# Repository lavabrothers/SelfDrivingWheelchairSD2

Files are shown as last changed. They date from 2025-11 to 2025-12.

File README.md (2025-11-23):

# SmartStride

Watch the video (https://youtu.be/vgjbnsrbdY0?si=ctMS2qIhK_sTW9yw)

*A quick, informal video showcasing the project.*

## Overview

SmartStride is an affordable, easy to use mobility upgrade system designed to retrofit existing electric wheelchairs with autonomous capabilities. The system integrates a Raspberry Pi 5-based control unit that processes data from a IMU and an infrared depth sensor (Kinect V2) to enable real-time obstacle detection and navigation. The goal of this project is to improve the mobility and overall safety of users with limited body control through intelligent motion assistance, all while maintaining an affordable cost and an easy-to-implement modular design. We designed the system around the Kinect V2, an inexpensive sensor array that is quite powerful compared to other sensors of its weight class. A good example is hospital settings moving patients around.

## Features

The system offers several modes of operation, controlled via a custom ESP32-based wireless controller:

- **Follow Person:** Using the Kinect's camera, the wheelchair will identify and follow the torso of an individual.
- **Autocruise:** The wheelchair cruises forward at a steady pace and stops promptly if an object obstructs its path. Once the path is clear, it continues cruising.
- **Manual Control:** Reverts to standard joystick operation, allowing the wheelchair to be driven manually, just as it was originally designed.
- **Mapping:** Utilizes the Kinect sensor's IR Flood Sensor to generate a 3D point cloud map of the surroundings by rotating the chair 360°.

## System Architecture

### Hardware

The system is built around a Raspberry Pi 5 as the central processing unit, which coordinates sensor inputs and motor controls.

- **Central Processing Unit:** Raspberry Pi 5
- **Depth Sensing & Vision:** Microsoft Kinect V2
- **Wireless Control:** ESP32-based controller with joystick
- **Orientation & Motion Tracking:** MPU-9250 (3-axis gyroscope, magnetometer, accelerometer)
- **Digital-to-Analog Conversion:** MCP4728 DAC to interface with the wheelchair's joystick port.
- **Power & Interfacing:** Four custom-designed PCBs for voltage regulation (12V, 5V, 3.3V) and comprehensive connectivity between all components via I2C

### Software

The software architecture is designed for dual-mode control, enabling both manual and autonomous operation.

- **Kinect Interfacing:** The open-source `libfreenect2` library is used to interface with the Kinect V2 sensor, providing high-definition color (RGB) streams, an infrared stream, and a Time-of-Flight (ToF) depth map.
- **Control Logic:** The Raspberry Pi runs scripts to handle both autonomous and manual control. In manual mode, it processes Bluetooth commands from the ESP32. In autonomous mode, it uses data from the Kinect to navigate and avoid obstacles.

## Installation

### Raspberry Pi (Wheelchair Side)

Follow these steps to set up the software on the Raspberry Pi.

1.  **Clone the Repository:**
    ```bash
    git clone https://github.com/lavabrothers/SelfDrivingWheelchairSD2.git
    cd SelfDrivingWheelchairSD2
    ```

2.  **Install `libfreenect2` (Kinect Driver):**
    The Kinect sensor requires the `libfreenect2` driver. Please follow the official installation instructions at [https://github.com/OpenKinect/libfreenect2](https://github.com/OpenKinect/libfreenect2).

3.  **Set Up the Python Environment:**
    Navigate to the `pi-code` directory to set up the Python environment.
    ```bash
    cd pi-code
    ```
    Create and activate a virtual environment (Make sure its Python3.11 or Python3.12):
    ```bash
    python3 -m venv .venv
    source .venv/bin/activate
    ```

4.  **Install Dependencies:**

    First, install the remaining packages from `requirements.txt`.
    ```bash
    pip install -r requirements.txt
    ```

    Next, install `pylibfreenect2` directly from the git repository, as it requires a special installation step.
    ```bash
    pip install git+https://github.com/r9y9/pylibfreenect2.git@40221e815c182ee31e8da33df717ccdef1bc615f
    ```

    *Note: If the above command fails, you may need to check if you installed libfreenect2 correctly. Sometimes you need to make sure the proper enviroment varaibles are set for your enviroment*

5.  **Install and Run the Service:**
    Navigate back to the root directory and use the `servicescript.sh` to install and start the main application as a systemd service. This will ensure it runs automatically on boot.
    ```bash
    cd ..
    sudo ./servicescript.sh install
    ```
    You can check the status of the service at any time with:
    ```bash
    sudo ./servicescript.sh status
    ```

## The Team

- **Matthew Itskovich:** Computer Engineering: Designed the ESP32 Code and Controller hardware
- **Evan Rees:** Computer Engineering: Designed Python Code and was Team Lead
- **Adam Lilly:** Electrical Engineering: Designed and Manufactured Regulators
- **Arturo Lara:** Computer Engineering: Admin Content and Soldering

## Project Media

**Longer, more detailed video:**
Watch the video (https://youtu.be/YJEAqcdVi9I?si=8ahl_1vFBt-6s-wN)

## Documentation

For more in-depth information, please refer to the following documents:

- **[Senior Design Conference Paper](./Documentation/Senior%20Design%20Conference%20Paper.pdf)**
- Additional written work on how this project works can be found in the `Documentation` folder.

## Map Example

**Demo Day Map:**
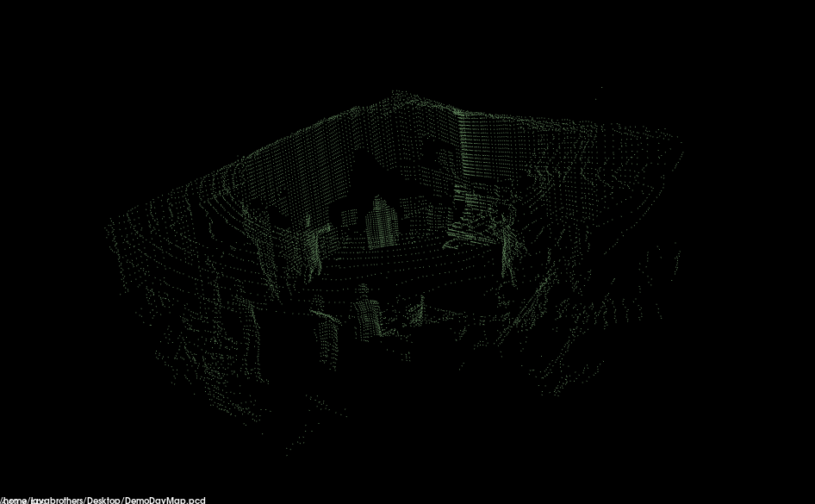
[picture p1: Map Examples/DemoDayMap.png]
Demo Day Map


## Acknowledgements

We would like to thank Dr. Chung Yong Chan and Dr. Arthur Weeks for their guidance and feedback throughout the SmartStride project. Their support and mentorship were invaluable in shaping the direction, design process, and successful completion of this project.

Thank you Dr.Wei for providing the wheelchair for use in this project.

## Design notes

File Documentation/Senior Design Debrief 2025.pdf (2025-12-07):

# Senior Design Fall 2025 Debrief

Hello! If your reading this then you have been given this wheelchair probably by Dr. Wei as a Senior Design Project for the future! My Name is Evan Rees and this was the first year we utilized and repaired this chair, so here are some lessons we learned that you can use in your iteration of a project!

Before I go into it too much, here is my contact information:
Email: ev596984@ucf.edu / evan@thereesgroup.com
Phone: +1 (941)-465-8774

If you every need some help getting antiquated or have a question that isn’t too easy to solve, shoot me a text/email and I will get back to you if I have a solution. No promises as I’m a student just like you and made a ton of mistakes and this chair still has a few unknowns. If we had more than two semesters then we maybe would have figured them all out ;]

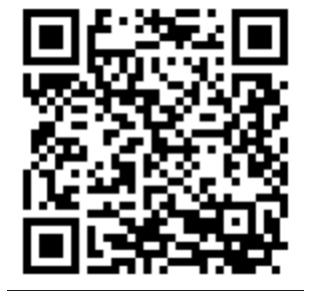
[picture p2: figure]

### SMART-STRIDE

This was our project for Summer/Fall 2025, you can access our website at: http://maverick.eecs.ucf.edu/seniordesign/su2025fa2025/g11/
or if that’s not your fancy we have a GitHub here: https://github.com/lavabrothers/SelfDrivingWheelchairSD2

Long story short we designed the wheelchair to move wireless and somewhat autonomously powered by a Pi 5, a 4 output DAC, and a Kinectv2 Sensor. All the code is made with these elements in mind, with a ESP32 as a wireless controller. It contains 4 modes:

- Wireless Manual Control Mode
- This mode basically just sends joystick inputs to the wheelchair, as if it’s plugged in directly
- Cruise Control Mode

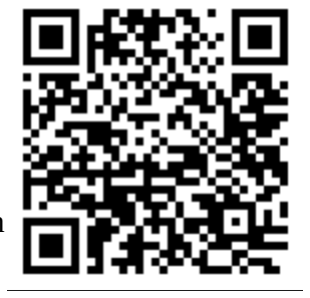
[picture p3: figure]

- This drives forward and will stop if it detects anything too close such an an object or a wall
- Follow Mode
- This will identify the closest person to the wheelchair, and attempt to
maintain distance from the person and keep them centered in it’s vision
- Map Mode
- This will spin the wheelchair 360 degrees and construct a depthmap of the environment around it

The GitHub has the most up to date info, but the website can get you an idea on how we progressed over the Senior Design Class. I recommend if you setup something similar, go to commit 22fafa5 as that has a bunch of crummy dev scripts you can use to test and experiment. However the repo is built in a way to do most everything already.

At time of writing I’m not sure if Dr. Wei will have you start your own project, or jump off the work we have already done, but if it’s the latter I have some ideas for you:

QR Code: GitHub

QR Code: Website

IDEAS
- Utilize the unused map mode to stitch together larger environments
- Fix follow mode to be more reliable and follow a single person without being stolen by another close person
- Assisted Manual Control that will help the user avoid obstacles while in manual mode
- Utilizing a rejected voice control mode (read back in the code commits), enable voice controls
- Integrate AI of some kind for natural voice commands
- Wei mentioned this to use when we initially were in development, but we ended up focusing on basic functionality
- (Very Hard) Create a Full Self Driving suite with the ability for a user to select a point in space and have it travel there

There! I hope those give some ideas on what to do, if not, good luck out there!

FIRST STEPS
Right now the wheelchair is not functional in it’s current form, that’s because you will need to give it two 12V Lead Acid batteries in series to tap into to power it. For testing you can use any 12V batteries, but probably a good idea to make them the same. If you want to get batteries that are perfect for the wheelchair, get 22NF class batteries.

For your convenience the levers in the back near the motors can be turned to allow for it to “free wheel” so you can push the wheelchair when it is powered.
MAKE SURE YOUR NOT IN FREE WHEEL BEFORE POWERING ON
THE CHAIR.

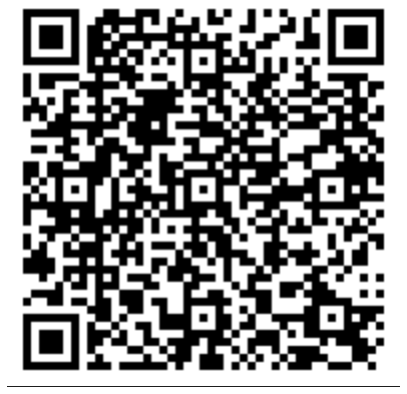
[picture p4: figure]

Refer to the physical manual there or digitized manual you can read. It’ll give you a basic idea on how to utilize the wheelchair in it’s original intended use. But if you want to use it differently you can use a similar method that we did.

Brain Slugging the Chair
While you could try to tap into the motors yourself, you should instead utilize the 1999 electronics inside to your advantage. Look over wheelchair_control.py we use to get an idea of how it works, but basically the joystick port can be manipulated to have the wheelchair move without needing to do anything special to the wheelchair’s electronics. The joystick port is located next to the blue potentiometer on the controller PCB. The order of the pins are as follows:

TOP
- Left Channel (WHITE)
- Right Channel (BLUE)
- Backwards Channel (BROWN)
- Forward Channel (YELLOW)
- Ground (BLACK)
- 5V Rail (RED)
BOTTOM

If you hook into the channel pins you first need to make sure each pin is 2.5V when booting up the chair, or else it won’t boot. And you must keep a ratio between the Forward/Backward and Left/Right Channels. So Forward Channel can be 3V and the Backward Channel can be 2V to move Forward.

QR Code: Old User Manual

Congrats, you can do whatever you want to the wheelchair. Feel free to refer to our Github to get any more insight and get access to our hardware schematics made in Fusion360. I highly recommend you test the wheelchair with fresh batteries to get an idea if it’s functional. Here is some roadblocks we hit that you should be aware of if you plan to follow in our footsteps

CAUTIONARY

- Since we need a 5V signal to the DAC, if your using I2C like we did with a Pi, you must use a Level Converter to ramp up the 3.3V I2C lines on the Pi to be accepted by the DAC
- The Kinectv2 is a computationally heavy device and requires USB 3.0. We overclocked our Pi 5 to 2.8Ghz and increased the USB buffer to a Gig. If you convert our python to C you maybe able to get more headroom, but consider accelerators or other SBC if you plan to do more on board the device.
- Alternatively design your 5V regulator to have a higher voltage to facilitate higher over clocks
- We used MobileNET-SSD, you may want to get an accelerator or get GPU acceleration working in your deployment
- If you fry the Pi, you will fry anything connected via the 5V rail like USB devices, do not fry your stuff. Trust me
- Get ahead of deadlines as this project is imense and hard to transport. The more you work eaely on the better.
- The Kinect sensor uses IR for depth, it maybe a bit spotty if there are IR night vision cameras so make sure you account for the interference like we tried last minute

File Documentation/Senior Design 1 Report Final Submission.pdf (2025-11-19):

## SmartStride

## The Future of Mobility: Hands-Free, Affordable, and Intelligent

## Midterm Report EEL4914 – Senior Design I Group 11

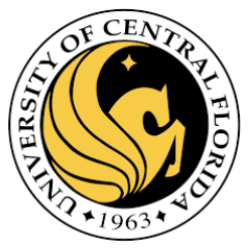
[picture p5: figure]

## University of Central Florida College of Engineering and Computer Science

## Matthew Itskovich, CpE Arturo Lara, CpE Adam Lilly, EE Evan Rees, CpE

## Reviewers: Sonali Das, Daniel Hedlund, Qun Zhou Sun, and Piotr Kulik Mentor: Chung Yong Chan

## Table of Contents

Table of Contents | 2
List of Figures | 4
Chapter 1 Executive Summary | 1
Chapter 2 Project Description | 2
2.1 Project Background and Motivation | 2
2.2 Existing and Prior Related Projects | 3
2.3 Objective and Goals | 4
2.4 Requirement Specifications | 6
2.5 House of Quality | 7
2.6 Project Diagrams | 8
Chapter 3 Research and Investigation | 11
3.1 Sensor Technologies | 12
3.1.1 Xbox Kinect V2 | 12
3.1.2 Lidar Sensor | 13
3.1.3 UltraSonic Sensor | 15
3.1.4 Comparison of Sensors | 15
3.2 Power Technologies | 16
3.2.2 Power Supply - Batteries | 20
3.2.3 Battery Level Indicator | 25
3.3 Processing Unit Research | 30
3.3.1 Raspberry Pi | 30
3.3.2 Nvidia Jetson | 33
3.3.3 x86 Computers: A Familiar Foundation with Significant Drawbacks | 35
3.3.4 Processing Unit Conclusion | 38
3.4 Wireless Processing Unit Research | 39
3.4.1 Communication technologies | 40
3.4.2 ESP32 | 41
3.4.3 Raspberry Pico W | 42
3.4.4 Arduino Nano RP2040 Connect | 42
3.5 IMU Chip Research | 44
3.5.1 MPU-6050 | 44
3.5.2 GY-9250 MPU9250 | 44
3.5.3 BNO055 Absolute Orientation Sensor | 45
3.6 LED Screen Research | 45
3.6.1 2.0" 320x240 Color IPS TFT Display - ST7789 EYESPI | 45
3.6.2 3.5" TFT 320x480 - HX8357D | 46

3.6.3 2.8" 320x240 ESP32-2432S028R | 47
3.6.4 Display Results | 47
3.7 Button Research | 48
3.7.1 Adafruit 560 | 48
3.7.2 APIELE Stainless Steel Push Button Switch | 49
3.7.3 E-Switch PR144C1900 | 49
3.7.4 Button Results | 50
3.8 3D Printed Material Research | 51
3.8.1 Solid Thermoplastic Filament | 51
3.8.2 Liquid Photopolymer Resin | 51
3.8.3 Printer Results | 52
3.9 Software Research | 52
3.9.1 Kinect Libraries | 52
3.9.2 LCD Programming Research | 53
3.9.3 ESP32-Display Program Research | 54
3.9.4 Button Reaction Program Research | 55
3.9.5 Buzzer Program Research | 56
3.9.6 Collaborative Code Platforms | 56
3.9.6.1 Git | 57
3.9.6.2 GitHub | 57
3.9.6.3 GitLab | 57
3.9.6.4 BitBucket | 58
3.9.7 Programming Languages | 58
3.9.7.1 Python | 58
3.9.7.2 C/C++ | 58
3.9.7.3 Coding Overview | 58
3.9.8 Repeatable Software Environments | 59
3.9.8.1 Docker | 59
3.9.8.2 Podman | 59
3.10 Digital-to-Analog Converter Research | 60
3.10.1 Analog Devices AD5664 | 60
3.10.2 Texas Instruments DAC7614 | 61
3.10.3 Analog Devices AD5696 | 61
3.10.4 Texas Instruments PCM4104 | 61
3.10.5 Analog Devices ADAU1978 | 61
3.10.6 Texas Instruments PCM1690 | 62
3.10.7 DAC Research Comparison | 62
3.11 AI Vision Models | 63
3.11.1 Kinect Skeletal Data | 63
3.11.2 RGB Object Detection | 64

3.11.3 Semantic Segmentation | 66
Chapter 4 Standards and Design Constraints | 68
4.1 Industry Standard Constraints | 68
4.1.1 Universal Serial Bus (USB) 3.0 Standard | 68
4.1.2 Bluetooth Standard | 70
4.1.3 LCD Screen Standard | 71
4.1.4 Button Standards | 72
4.2 Practical Constraints | 75
4.2.1 Time | 75
4.2.2 Economic | 76
4.2.3 Environmental | 77
4.2.4 Ethical | 77
4.2.5 Adaptation of Current Wheelchair | 78
4.3 ADA Constraints/Compliance | 78
4.3.1 ADA Physical Dimension Constraints | 78
4.3.2 ADA Visual Constraints | 80
4.4 Personal & Mission Constraints | 81
Chapter 5 ChatGPT and other Similar Platforms | 83
Chapter 6 Hardware Design | 89
6.1 Power Supply Systems | 89
6.1.1 3.3V Regulator | 89
6.1.2 5 V regulator | 90
6.1.3 Battery Level Indicator | 91
6.2 Interfacing with WheelChair PCB | 93
6.3 Wireless Controller Schematic | 93
6.4 Pi DAC & Power Delivery | 95
Chapter 7 Software Design | 97
7.1 Emergency Stop Button | 97
7.2 Selfdriving/Cruise Control Algorithm | 98
7.3 Joystick Workflow | 100
Chapter 8 System Fabrication/Prototype Construction | 101
8.1 PCB Fabrication | 101
8.2 Controller Casing Prototyping | 101
8.3 Sensor Casing/Mounting Fabrication | 102
8.4 Pi to DAC & Power Delivery PCB | 102
8.5 Wireless ESP32 Controller PCB | 104
Chapter 9 System Testing and Evaluation | 105
9.1 Hardware Testing | 105
9.1.1 LCD Screen Testing | 105

9.1.2 Button Testing | 106
9.1.3 Buzzer Testing | 106
9.1.4 Battery Testing | 106
9.1.5 Motor Testing | 107
9.2 Software Testing | 110
9.2.1 LCD Screen Testing | 111
9.2.2 Emergency Stop Testing | 111
9.2.3 Freenect2 | 111
9.2.4 ESP32 BLE Server | 113
Chapter 10 Administrative Content | 114
10.1 Project Milestones | 114
10.2 Budget Estimates | 116
10.3 Division of Labor | 117
Chapter 11 Conclusion | 119
Works Cited | 121
Appendix | 124
List of Images | 129

## List of Figures

Chapter 1 Executive Summary
Chapter 2 Project Description
2.5.1 House of Quality | 7
2.6.1 Hardware Diagram | 8
2.6.2 Software Diagram | 10
Chapter 3 Research and Investigation
3.1 Sensor Technologies
3.1.1 Kinect V2 | 12
3.1.2 Lidar FHL-LD20 | 14
3.2 Power Technologies
3.2.3.1 Battery Voltage Regulator | 25
3.2.3.2 LM324 Battery Indicator | 28
3.6 LED Screen Research
3.6.1.1 ST7789 EYESPI | 45
3.6.2.1 HX8357D | 47
3.6.3.1 2432S028R | 48
3.7 Button Research
3.7.1.1 Adafruit 560 | 49
3.7.2.1 APIELE Push Button | 50

3.7.3 E-Switch | 50
3.9 Software Research
3.9.2.1 Flow of Information | 55
3.9.4.1 Button Program Example | 56
3.9.5.1 Buzzer Program Example | 57
Chapter 4 Standards and Design Constraints
4.1 Industry Standard Constraints
4.1.1.1 xkcd Standard Comic | 69
4.3 ADA Constraints/Compliance
4.3.1.1 ADA Floor Space Diagram | 80
4.3.1.2 ADA Clearance Chart | 80
4.3.1.3 ADA Knee Clearance Chart | 81
Chapter 6 Hardware Design
6.1 Power Supply Systems
6.1.1.1 3.3V Regulator | 91
6.1.2.1 5 V regulator | 92
6.1.3.1 Battery Level Indicator Schematic | 93
6.2 Interfacing with WheelChair PCB
6.2.1 Original Controller PCB | 94
6.3.1 Wireless Controller Schematic | 95
6.4.1 Pi to DAC & Supply Schematic | 96
Chapter 7 Software Design
7.1.1 Emergency Stop Visual | 98
7.1.2 Button Programming Diagram | 99
7.2.1 Self Driving/Cruise Control Algorithm Flowchart | 100
Chapter 8 System Fabrication/Prototype Construction
8.3 Sensor Casing/Mounting Fabrication | 102
8.4 Pi to DAC &

## Chapter 1 Executive Summary

While cures for diseases and medical technology continue to advance, there are still many individuals out there that suffer from irreparable damage that has made their daily livelihood far more difficult than the average person. Some people become weaker and others will unfortunately lose abilities that most people take for granted such as being able to walk without the assistance of any medical apparatus. As much as we wish we could, we can not provide a cure to debilitating effects like paralysis, but with dedication and ingenuity we can make the tools most people have at their disposal to make their lives just a little bit easier. This project, SmartStride, is a means of converting both old and new motorized wheelchairs into a new and more accessible means of transportation for the mobility impaired. With the addition of modern day computers and sensors we can provide a cheap and efficient means of automating the movement process for those in need of an easier to use wheelchair.
The SmartStride wheelchair project has two main focuses, the first is to design a way to revamp old wheelchairs or to adapt newer, more modern, wheelchairs to be compatible with the systems we are using to collect and process data. This includes adding an entirely new function to the chair, that being an automatic movement setting. This automatic mode will allow users to set the directional inputs of their desired destination, so that those that have trouble controlling the chairs motor functions can have a more accessible option of navigating their environment. This of course will require the addition of multiple computers to be installed so that we can ensure the chair has the processing capability of taking in directional input while being able to accurately move the chair with the motors. The refitting of the chairs controllers will also need to occur as a new layout and visual informational outlet will need to be installed to ensure that the user can manage the system and receive any information regarding the current status of SmartStride’s functionality.
Along with updating the hardware and improving the functionality of the wheelchair SmartStride will also be incorporating sensors to the chair that will be used in tandem with the automatic movement mode. This is to ensure that the safety of the passenger is not compromised by the chair’s inability to perceive any dangers around it, or to identify if the route the wheelchair is trying to take is blocked or not. One of the sensors that will be used in our system will be that of Microsoft’s Xbox Kinect camera, a surprisingly advanced piece of hardware that incorporates multiple types of sensors besides just a visual input. With this piece of technology we can easily scan the user's surroundings and find distant objects that may or may not prove to be a threat to the automatic systems of the chair. This document contains all the information collected for the project along with all the work needed to have SmartStride fully operational. It lists a collection of components and information used in the process of designing the wheelchair along with the overall cost of building it.

## Chapter 2 Project Description

This chapter provides a detailed blueprint for the SmartStride project, an initiative focused on augmenting an existing electric wheelchair with affordable, autonomous capabilities. We begin by exploring the project's background and motivation, establishing the need for a cost-effective, intelligent mobility solution. An analysis of prior related projects will then be presented to contextualize our design choices. Subsequently, the chapter outlines our specific objectives and goals, followed by detailed requirement specifications for the system's core components. To conclude, we will present a House of Quality analysis and high-level hardware and software diagrams that illustrate the proposed system architecture and operational logic.

## 2.1 Project Background and Motivation

Ever since the earliest humans started walking earth, there has been an issue at play for the physically disabled to get around in a smooth manner. This issue has posed as an attempt for engineers since the beginning of the occupational concept to come up with a solution for the handicapped. One of the best-known solutions engineers have come up with to date is the wheelchair. The first ever case of the wheelchair seems to come in as early as in 12th century Europe, but the first ever documented case happened in the 17th century in Germany. The German maker of this wheelchair, Farffler, initially created these three-wheeled contraptions for the wealthy [1]. Over time, the design of the wheelchair has gotten a lot more optimal; they have gotten very expensive as well.

A more specific optimal design we want to focus more on here is the electric wheelchair. The earliest known case of the design was in 1953. George Klein and his fellow companions wanted to make a motorized wheelchair mainly to help injured veterans on their return home from WWII [2]. Ever since 1953, the electric wheelchair has continued to change drastically in both its features and in its popularity. It grew in popularity so much that even the World Health Organization declared access to the motorized wheelchair a basic human right. Even though the electric wheelchair is now declared a basic human right and people can get them for cheap or even free through government assistance programs and charities, there is still a big problem at hand for people that don’t have access to them because of the costs.

While the issue of affordability is present in electric wheelchairs, there is always room for improvement in the design. A very useful improvement would be to have a smart autonomous electric wheelchair that helps the user to avoid obstacles without even having to control it. This idea is what our group intends to work on. The name we came up with for our project is the SmartStride. The SmartStride would be useful in the sense that it will empower users with severe disabilities as well as for it to enhance safety and navigation.

The motivation behind wanting to create an automated electric wheelchair stems mainly from our want to help people with disabilities. There are a lot of similar and well documented projects out there but it seems like the optimality of the designs could always be improved. Another big reason we would like to create a functioning smart wheelchair is due to the already high costs. An electric wheelchair without any smart features on the lower tier level starts around $1,500 and only goes up from there. Our group aims to design a smart wheelchair that’s
affordable | enough | to | be | accessible | to | people | in | lower-income
communities—something we believe would be deeply meaningful and fulfilling!

## 2.2 Existing and Prior Related Projects

The good thing about our project idea is that there have been a lot of attempts at creating an electric wheelchair. There have also been so many attempts at it that Vocic.com even created an article walking people through the basics of how to convert a manual wheelchair to an electric wheelchair. In the article, they lay out different ways of implementing this idea. The different ways are installing a front-powered wheel, wheelchair conversion kit, joystick control system, power assist system, full electric conversion, and DIY conversion. Also in the article, they lay out costs and different safety measures (legal) that should be taken into consideration when designing this project [3]. We will be starting with an already designed electric wheelchair so we won’t need to change out the hardware too much.
We came across different project ideas online. One electric wheelchair project that captured our attention was created by a team of engineers at UC Davis. Their project is called the DIY Electric Wheelchair, and they put a big emphasis on creating a cost-effective wheelchair, which is what our team is trying to do. This wheelchair is not automated but it is a good reference for hardware. On their official website, they have a bill of materials that shows all of what they bought. Some important things we noted that we may try to add to our design are a 12 V battery and 12V DC brushed motor. The BOM for this project came out to a little over $2,000. While $2,000 is particularly on the cheap end of the electric wheelchair spectrum, our goal is to keep the chair under well under $2,000. On the team’s project website, they highlight their needs of three different regions of the wheelchair: The power chain needs, body needs, and overall needs. The power chain highlights the overall motor's abilities, ability to climb road curbs, and good acceleration. The body needs show the teams want to have a durable wheelchair that can meet the ADA specifications. Overall needs are very similar to the other two types of needs. This section of the website is very useful for us to organize what we are looking for in our design [4].
Another project we found that is like what we are trying to do comes from a team at Rutgers university. They created a conversion kit that attaches to a manual wheelchair frame to turn it into an electric one. Even though this wheelchair isn’t an automated one, it is a good reference for what parts we are going to use for our project. It consists of two motors and a control system that is user-friendly. The motors are directly attached from the bottom frame to each of the wheels. One thing that stood out to us about this project is that the team was able to keep their budget within $750, which is where we’d like our total cost to be when we start demoing our prototype. This team’s project report does a really good job of laying out the control system diagram showing how the remote flows to the Arduino, then to the batteries, and finally to the motors to control the wheelchair. The team also lays out torque calculations for different surface types and then designs the wheelchair around that. They also do horsepower calculations. The torque needed for a standard concrete wheelchair ramp calculated is 2.5815 ft-lbs. Other important calculations they laid out are horsepower needed for an appropriate range of torque and RPM. The desired speed of a wheelchair according to their project came out to about 2 feet/second which equals about 754 rotations per minute. These types of calculations in their report gave our team an idea of how to properly gauge what type of motors and the voltage batteries we are going to need to be able to power our wheelchair given different variables (slope, weight of load, terrain type) we need to consider. When trying to do research on autonomous wheelchair designs, it seems like a lot of companies have severely invested in these types of projects and have come out successful. One smart wheelchair design that stands out is the Mobilis Autopilot, located out of Poland. This company takes existing wheelchairs and helps people to convert their wheelchairs into a smart AI assisted chair that you can even control and modify all by just using your smartphone [5]. The autopilot feature on the wheelchair is an AI assisted feature that uses a camera on the wheelchair to automap things nearby. For example, if someone ventures into the living room with their chair, the chair will self learn how to map out objects in the living room and avoid them for the future. The user can use their smartphone to set up and name desired destinations as well as. When thinking about how we want to focus on our own automated electric wheelchair, the Mobilis is a good reference point for the basis of our project research.

## 2.3 Objective and Goals

This project’s basic idea is to augment an existing electric wheelchair and give it auto driving capabilities. Since we are modifying a broken chair (dead battery) we also plan to restore it to working condition. This can be useful for automating movement and making automated safety features, particularly for users with vision impairments. We also hope we can make this system affordable, so that other users can do this cheaply themselves. As well as give it intuitive user features that can be easy to control and preferable than bypassing the system.

Overall Goals
- A modular design that can be easily maintained

- Cost effective
- Maintain feature set of base wheelchair

Basic Goals
- Be able to drive forward automatically
- A user can define speed and it can basically “Cruise Control”
- Be able to detect and stop at an obstacle
- If it detects a obstacle, it will stop and alert the user
- Manual override button
- This button or function will stop the system and allow for user correction
- Battery level estimate and time estimate
- Either via a screen or LED array we can show the battery level, as well as a time estimate till empty

Advanced Goals
- Automatic Rotation from obstacle
- Able to detect and point chair away from the obstacle
- Incline Detection
- The Chair can detect the incline and juice the motors based on incline
- Edge Detection
- Be able to detect curbs or sharp drops and prevent driving
- Auto driving from point A to B (Stop at Obstacle)
- We can set the chair to move to a location via a predetermined route, stopping when that route is disturbed
- Bluetooth control
◦A controller, via bluetooth, can allow for the user to control and set commands for the system
- Tool-less or minimal tool battery replacement
- Since the battery is a consumable part, we hope the battery can be made in a way that it can be replaced or upgraded

Stretch Goals
- Dynamic Routing
- When auto driving from A-B, a user doesn’t need to define a path and the system will navigate to it
- Obstacle avoidance and bypassing
- The system should be able to detect an obstacle and drive around it without user interaction
- Doorway alignment
- The chair can detect a doorway and align with it and drive through
- Unauthorized Braking

- If the user has an unwanted person trying to push the chair, the brake will engage. Or if the chair is on a steep incline and the user doesn’t want to movement

With these goals in mind, outside of the basic goals, we may not get to all of them. However to make a fully competent Wheelchair driving system, comparable to other self driving systems these goals must be understood and pursued. Our hope is to provide a system that is useful for users with limited range of motion or vision

## 2.4 Requirement Specifications

Motor Requirement Specifications:

- Should support a load of 120 kg (including user and chair).
- Should enable a top speed between 4km/h
- Must be capable of climbing a ramp with a gradient of up to 5 degrees.
- Must operate quietly with noise levels not exceeding 50 dB.
- Should have thermal protection to prevent overheating above 120 degrees Fahrenheit.
- Motor casing should be weather resistant
- Each motor must weigh less than 5kg.
Controller Requirement Specifications:
- Must provide smooth acceleration and deceleration without jerks.
- Should support speed modes: slow, normal, and fast.
- Should include over-current, over-voltage, and thermal protection features.
- Response time to input signals should be less than 200 milliseconds.
- Should integrate with a 24V to 36V battery system.
- Total controller unit must weigh less than 1.5 kg
Control Unit Requirement Specifications:
- Should allow operation via joystick
- Must have user-friendly interface for either impaired and non-impaired users.
- Joystick/controller response delay must be less than 300 milliseconds
- Must support Bluetooth connectivity for remote operation (range>= 6 meters).

- System should log basic usage data (speed, battery level).
- Should be able to operate continuously for at least 60 minutes on full charge.
- Control unit housing should be rugged and lightweight, under 1 kg.

## 2.5 House of Quality

Our House of Quality is a diagram that will help guide us through what may be complimentary or against each other. This allows us to visualize what solutions will be engineered to work with each other, or what tradeoffs we need to consider. Hopefully when we use this, we can find a nice balance between what we want and what we can achieve.

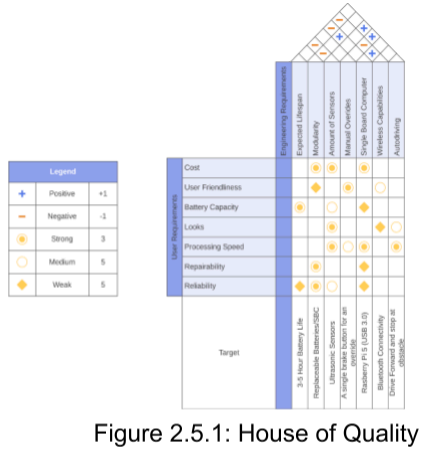
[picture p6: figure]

## 2.6 Project Diagrams

These diagrams are the basic outline of how the wheelchair will be constructed and connected together. It is intentionally high level to give a general overview and guidance to how the whole system is put together. The diagrams give us:

## Hardware Diagram

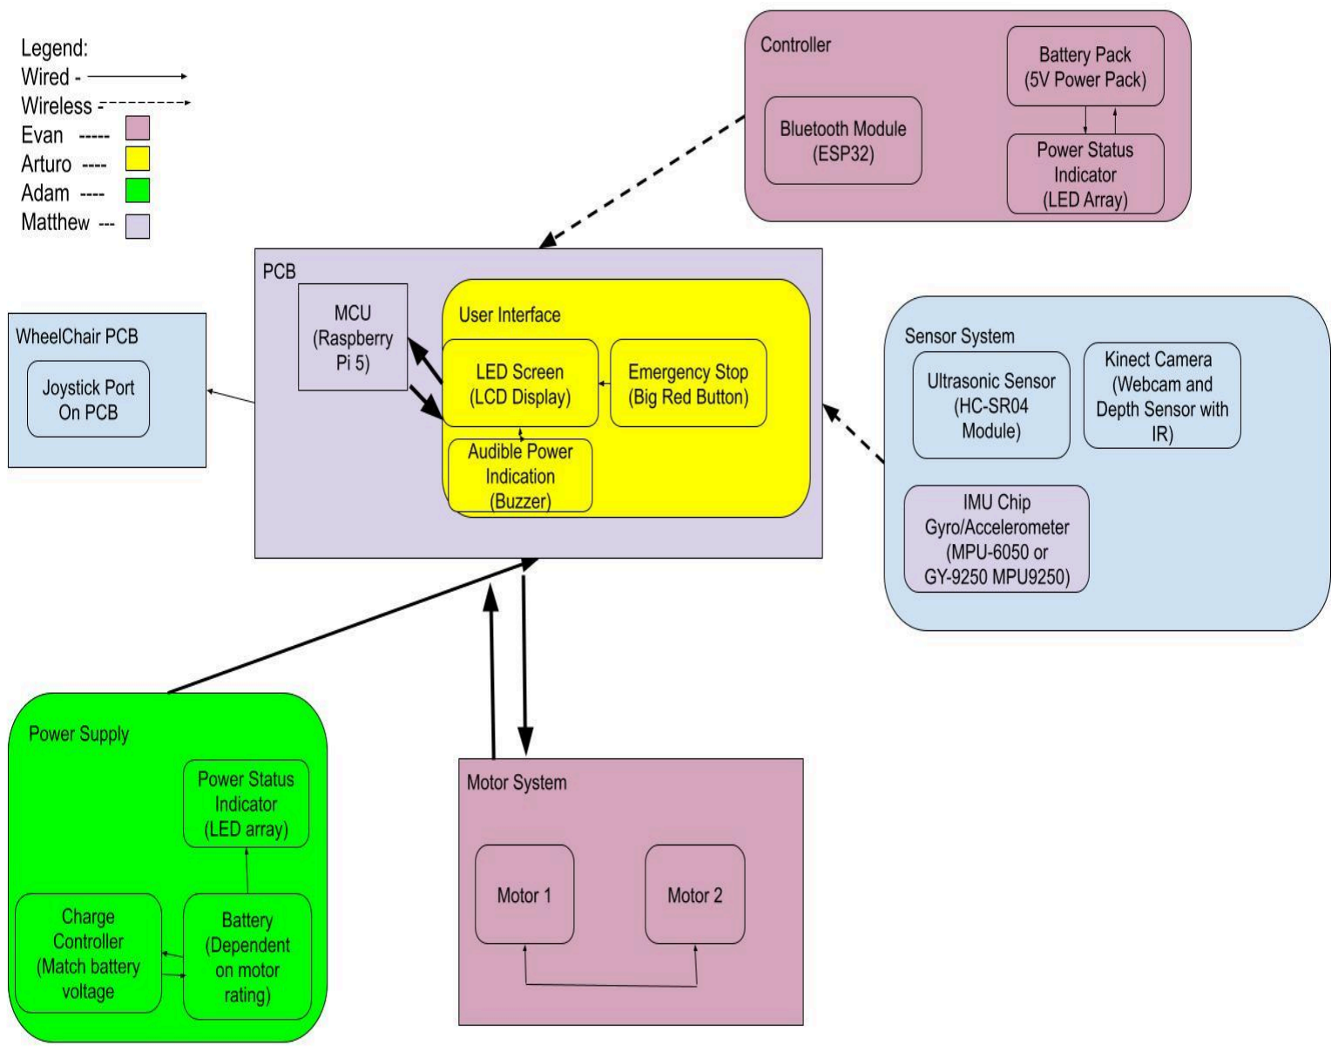
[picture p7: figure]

Figure 2.6.1: Hardware Diagram

The diagram above explains the hardware architecture of the system. The main core of this diagram is the MCU (Raspberry Pi 5) which serves as the central processing unit and performs all operations. The hardware systems performance is divided into many interconnected blocks. The user interface provides interaction points with the user which features an LED screen for visual feedback, a buzzer for notification, and an emergency stop button feature. Both the user interface and the MCU will be hooked up on the PCB. Connected to the PCB will be the joystick interface where the user can manually override the autonomous working wheelchair to control it themselves.
A system of sensors will be located throughout different places on the wheelchair. This system will consist of an ultrasonic sensor (distance detection), IMU Chip (gyro/accelerometer), and Kinect for more advanced visual and depth sensing. All of the data from the sensors will be sent to the MCU for processing. From there, the MCU will give commands to the two motor system based on the data. The power supply will power the whole system. The power supply features two 12V batteries, a charge controller to charge the batteries, and a power status indicator to track the current charge of the batteries.
Additionally, on the chair, located on the right arm is the controller block. Here, the bluetooth module will be hooked up as well as the joystick. The bluetooth module will be wireless communication for the user interface and external devices. A 5 V battery pack will be placed in this to power all of the components inside the controller. Lastly in the controller, a visual display will be shown to the user of the current battery charge.
As one can see from the graph, the color coding represents who in our team will research and work on the certain parts of the project. The dashed and solid lines represent whether the connections between the components and the MCU are wired or wireless. As one can see, most of the connections will be wired. Overall, the design emphasized user interaction, environmental awareness, and robust motor control, all managed by the central Raspberry Pi.

## Software Diagram

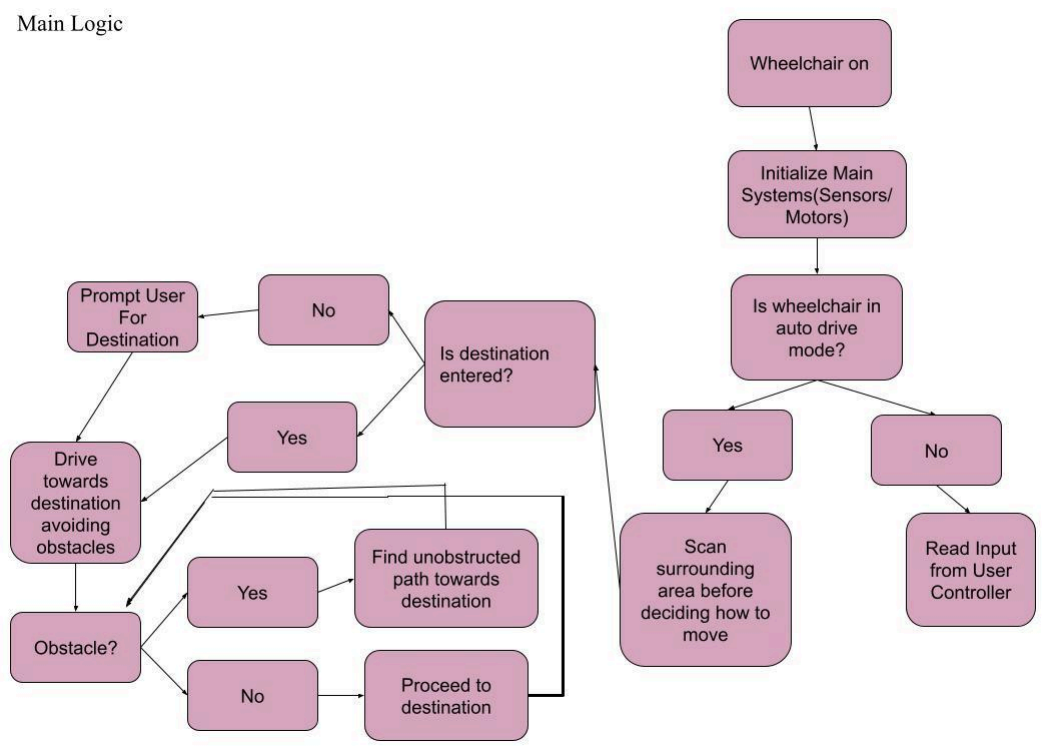
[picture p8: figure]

Figure 2.6.2: Software Diagram

The diagram above shows the min software logic for our wheelchair described in a simple form. The logic begins when our wheelchair turns on which leads to the initialization of the main systems. After initialization, the system checks whether the chair is in auto-drive mode or not. If it is not in auto-drive mode, the wheelchair operates under direct user input. If the wheelchair is in autodrive mode, the system will first scan the surrounding area before deciding how to move. After the scan, then the system will have the user input a destination. If no destination is entered after a certain amount of time, the system will prompt the user to enter a location. Once a destination is entered, the system attempts to drive towards the destination while avoiding obstacles. During the driving process, the system continuously checks for an obstacle. If an obstacle is detected, then the system will scan and try to find an unobstructed path with the sensors. If nothing is detected, then the wheelchair will continue along its path already set in place. This marks the end of the software logic sequence. Overall, this diagram is very clear to understand and easy to implement.

## Chapter 3 Research and Investigation

Research is the foundation upon which our project decisions are built. Before moving into design or implementation, it is critical that we fully explore the landscape of existing technologies, approaches, and user needs. This chapter serves as a comprehensive investigation into the tools, systems, and methods that will inform our project direction. Through systematic research, we ensure that every decision is grounded in evidence, technical feasibility, and relevance to the user experience.

We begin by examining the key components and concepts central to our design goals. This includes reviewing similar mobility systems, comparing hardware and control schemes, and evaluating past efforts in the development of accessible wheelchair technologies. Our goal is not to reinvent what already works, but to understand what has been done and build on it more effectively. Research also provides the data needed to avoid inefficiencies. Without a structured investigation, we risk making assumptions that lead to ineffective solutions or technical limitations down the line. Whether analyzing motors, joystick responsiveness, or structural modifications, this chapter ensures our decisions are data-driven and backed by engineering best practices. Ultimately, this chapter sets the intellectual groundwork for the design process that follows. The insights we gather here will directly influence our prototyping strategy, component selection, and system integration in the next phases of the project.

## Hardware Research

When thinking about the scope of the research for this project, hardware research is going to take up the bulk (if not all) of the budget we set for the project. When researching our hardware, we will focus on the power supply, pcb design, controller, sensor, and the user interface. Some of these components will be more straightforward to research than others such as the power supply and motor system. While going through the research for our hardware, we want to keep in mind the requirement specifications in the overall design as well as the budget. Another big thing to keep in mind while doing research is the quality and durability of each component needed to withstand certain factors like outside temperature, load power, vibration, and UV exposure. Lastly, while doing hardware research, the most important thing to keep in mind is that the components that are being researched on to be put into the design user friendly and meet safety standards as outlined by the IEC 12184: International Standard for Electric Wheelchairs.

## 3.1 Sensor Technologies

Since we are making a Self Driving Wheelchair, we need to start with finding out what sensors we need. They are our eyes to the world and if we want to be able to detect obstacles then we need adequate sensors that are versatile and accurate. We also looked into self-driving cars, and the sensor arrays they use.

## 3.1.1 Xbox Kinect V2

When looking into sensors, we found we needed to find a way to find depth so that we can detect how far an object is. We also wanted a way to detect how many objects, as well as map out the environment around the wheelchair. We turned to sensors that we knew of, however one team member had a Xbox Kinect v2. This gamer peripheral has a history of being used in research and experimental settings, as it had quite advanced sensors integrated into it at an affordable price. This sensor array has 2 high quality sensors:
- A RGB 1080p 30Fps Camera
- A 512x424 Pixel 30Fps IR Depth Camera
- Operates from 0.5 meters to 4.5 meters of distance
- Has a FOV of 70 degrees horizontal and 60 degrees vertical These two sensors are quite helpful, mainly the depth sensor. A benefit of this implementation is that it is widely documented and used, whilst also having the RGB camera that can be used for image recognition and such. It also takes a power input of 12V, which is advantageous as will be discussed later.

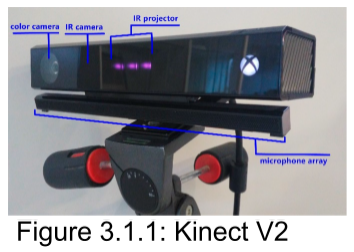
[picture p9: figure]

When deciding on a sensor we also need to decide a sensor with software that can utilize it. We won’t go into detail here and will list technologies in the software portion but it can utilize many popular libraries that utilize the depth sensor. This is the more useful portion of the sensor, as we can recognize and measure our surroundings with remarkable detail. This comes at the cost of requiring a powerful processing unit to ingest the data produced by the sensor, as it requires OpenGL acceleration to function and most embedded systems would struggle with it. We also require a USB 3.0 connection at a speed of 5Gbps. If we don’t have a sufficient CPU and a fast enough data interconnect, the sensor will not provide data properly and will not be helpful for a real time sensing such as self driving.

Related Kinect Projects

Advanced RealTime Road Detection and Autonomous Vehicle Control using Convolutional Neural Networks and Human Learned Driving Models

This project uses some fairly low tech practices to make a self driving ATV. However it fully utilizes the features of the Kinect v1, a similar but less powerful version of the Kinect v2. It utilizes both Vision and AI data to make a fully self-driving vehicle with self steering, variable speed, and utilizes AI models for decision making. This project is more sophisticated with its self-driving algorithm than planned for our project, utilizing AI for vision analysis, but is a very good example of the sensor’s use in an application like ours. The reason we will not use the Kinect the same way as this project is due to the power hungry GPU required to run the AI models necessary for vision based detection. Since we are trying to minimize power consumption this would not be a direction we can follow. It is a very interesting project however and some of it’s discoveries may be useful for our project

https://github.com/sieuwe1/Advanced-Real-Time-Self-Driving

Self-Driving Wheelchair (Graduation Project)

This project is entirely in software, and has code and ways to implement the Kinect if you were to recreate this project in the real world. It also uses a wheelchair design and was a graduation project interestingly enough. Unfortunately it doesn't seem to be easily adapted nor very helpful for our specific use case. However it shows a cool example on how we would use sensors to map out an area.

https://github.com/YousifAdel170/Autonomous-Wheelchair

### 3.1.2 Lidar Sensor

Lidar is a sensor type that is quite new compared to Ultrasonic and IR. LIDAR stands for Light Detection And Ranging. Lidar uses many small light dots to map out an area with depth and color. It’s used in a variety of applications, such as:
- Surveying

- Such as geological surveying or geography mapping
- Satellite imaging
- Seismology
- Global Mapping
- Laser Guidance
- Drone Guidance
- Height Detection
- Surveillance
Most interesting for our case is for self-driving applications. It’s very helpful for self driving implementation as the light dots are not impeded by bad weather conditions and have quite a high resolution. The specific model that we are considering is a 360 degree sensor model FHL-LD20. 360 Degree sensors are common on many advanced self-driving cars like Waymo. This sensor spins at 60 rpm giving a fairly fast mapping at 6 times per second. However this is a 2D

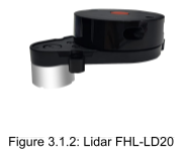
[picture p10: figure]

sensor, which means it is both cheap but has a limit in scope of vision. There do exist 3D sensors but are quite expensive, and for our cases will not be necessary for our self driving implementation. It will sense depth of a single point every degree around us, this will be useful for finding the distance of obstacles in a 360 view around us. This is a 8 meter range around the wheelchair, which is perfect for a wheelchair where obstacles shouldn’t be encountered very quickly, but in a self driving high speed vehicle.

Another benefit is this sensor uses Pins to communicate and require much less data throughput. Where other sensors will send lots of data down the data lanes, this uses UART and simpler data delivery. This is fantastic in comparison to the Kinect from the previous section, which requires as much as 5Gbps of data throughput to function properly.

### 3.1.3 UltraSonic Sensor

The UltraSonic sensor is a simple sensor that is the lowest tech sensor in this comparison. It also has the lowest range of the other sensors at 450 cm of effective maximum distance. However, like Lidar and the Kinect, it provides accurate depth data of the closet object in a 30 degree FOV from the sensor. This could be helpful in making a simple virtual “bumper” so that if another sensor fails to detect an obstacle we can use its input as a last resort. It can’t create a map of its environment like the other sensor mentioned, but its data can still be helpful and is used alongside many self-driving systems. The technology even exists in current cars for crash detection. As such it's a perfect sensor that can be implemented into our project. It also has a very low power draw, which is perfect for our battery operated system that cannot be tethered to the wall. It also has an extremely fast response time, making it perfect in the real time system we are programming in.

It is also a very popular sensor with much documentation on how it works. We also used them in Junior Design for our distance sensor, so our team has familiarity with the sensor. In fact, we have a few in our possession which means we can reduce costs if we only require a few. Though they are remarkably cheap and easy to implement, thus they are a perfect supplemental sensor.

They are also remarkable low powered and easy to wire, so making edge sensors paired with wireless low powered systems is ideal. They have limited FOV so we will need many of these supplemental systems to be effective, or to fill in holes other sensors have issues seeing

### 3.1.4 Comparison of Sensors

With all these sensors in mind, we decided to go with the Kinect Sensor as our main sensor. Even though we may use the other sensors as supplemental, the kinect is so much more cost efficient for how much data we can use that it will become the backbone to our sensor system.

Table 3.1: Tech Comparison of Sensors
Criteria | Kinect v2 | Lidar | Ultrasonic
Cost | ~$10-$40 | ~$45-$150 | $2.50
Range | 0.5m to 4.5m | 0.1m to 8 m | 10cm to 450cm
Resolution | IR 512x424 pixels | 0.8cm | 0.3cm
Power Consumption | 32 Watts | 0.3 Watts | 0.1 Watts

FOV | 30 Degrees | 360 Degrees | 70 Degrees
Frequency | 60 hz | 6 hz | 100000 hz
Link | https://www.ebay.com/sch/i.html?_nkw=kinect+v2&_sop=12 | https://a.co/d/1tH BdP7 | https://a.co/d/5wJ WHeX

## 3.2 Power Technologies

When designing the SmartStride, it is very important to keep in mind how the power will be supplied to the hardware components. While supplying power, we needed to determine how to regulate the output to prevent damage to components and ensure efficient power management for long-term product reliability. This section will figure this out and in the process will talk about voltage regulators, batteries, and battery level indicators.

### 3.2.1 Voltage Regulator

The two batteries that will be supplying all the power to the wheelchair will fluctuate a bit in terms of their voltage. Both batteries are connected in series meaning the total voltage will be around 24 V. When the two batteries are fully charged, the voltage can fluctuate 1 to 2 volts higher. If there is a moderate load that the batteries have to supply to the wheelchair, the voltage won’t be right at 24V. More likely, the voltage being pushed out will be somewhere between 22.5 V and 23.5 V. If there is a heavy load, especially if the wheelchair user puts the chair at full speed, the voltage may fluctuate even more to somewhere between 20 and 21 V. With the voltage of the batteries fluctuating a lot, this creates a problem for all of the components hooked up to the SmartStride. Components such as the Kinect need a stable voltage. If it gets a fluctuating voltage, it may fry the internal system within the component rendering it unusable. To address this issue, we will need to create voltage regulators for each additional component on the wheelchair as a precaution.

There are many types of voltage regulators. When choosing one, we need to ensure it can maintain a constant output voltage, whether the battery supplies more or less than the nominal level. Also, it is important to keep in mind that we are working with DC voltage so we don’t need to look into any types of regulators that convert AC to DC. Since the voltage from the batteries can vary widely depending on the load, having a regulator in place helps prevent that fluctuation from reaching sensitive components. This ensures that all devices receive a consistent and reliable voltage during operation. Shown below are the types of regulators we looked into, as well as the final selection and an explanation of why we chose that type:

## Linear Regulators

A linear voltage regulator in short terms is a device that makes sure there is a constant DC output voltage for any difference with the load conditions or input voltage. This type of device will use a BJT or MOSFET which is controlled by an op-amp usually. The linear voltage regulator acts as a voltage divider to get the regulated output voltage. This type of regulator is also called a step-down converter because the output voltage is always less than the input voltage. This regulator would definitely help in our project, but its downside is that it is not ideal for us because we also need to protect our components from low voltage. Getting more into linear voltage regulators, there are two main types: a series voltage regulator and shunt voltage regulator. The series regulator controls the voltage by placing a transistor in series with the load. The series acts like an automatic potentiometer that adjusts its resistance to maintain the constant voltage at the output. The shunt regulator works by placing the regulating element in parallel with the load. A constant output voltage is kept by “shunting” the extra current away from the load by adding a transistor to ground. If we were to pick a linear regulator for the project, we would definitely choose the series regulator because it is more efficient and doesn’t need extra power supplied to it like the shunt type, just to be wasted If we were to select a linear regulator for the project, we would opt for a series regulator due to its greater efficiency and the fact that it does not consume additional power unnecessarily, unlike the shunt regulator.

## Switching Regulators

What makes a switching regulator different from a linear regulator is that a switching type turns off and on a component like a MOSFET to carry out the voltage conversion. Switching regulators are available in three main types: Boost, Buck, and Buck-Boost. Boost regulators are the case for when you want the input voltage less than the output voltage. Buck regulators are the opposite of boost regulators where the input voltage is greater than the output voltage. Using a Boost or a buck regulator would be nice for the SmartStride but they aren’t ideally what we are looking for because the regulators only regulate the output voltage for either the case of the input voltage being higher, or lower than the output voltage, not both at the same time. The third type of switching regulator is the buck-boost regulator. It is a mix of both the buck and boost regulator, hence the name. A buck-boost regulator maintains a stable output voltage regardless of whether the input voltage is higher or lower than the desired output voltage. This is the type of regulator that most aligns with our goal of protecting the components on the chair from getting fried from the unstable output from the batteries.

Table 3.2: Tech Comparison of Switching Regulators

After comparing the three different switch regulators above, we decided to go with the buck-boost regulator. Our reasoning for picking this component was due to the operating range. It was a must have for the components on the SmartStride to be protected by both undersupplied and oversupplied voltage. There are some setbacks from choosing this component over the other two. One setback is the maintenance. The buck-boost regulator has many more components than the buck and boost regulators. More components means a bigger possibility of something going wrong with the regulator. The good thing is we can buy in bulk for this type of regulator just in case if anything goes wrong, that way we have many back ups.
Another downside of this type of regulator is that it is the most expensive out of the three. The regulator ranges in price depending on the current capacity it needs and the range of input voltage that is expected from the fluctuating power supply. Most of the components we will be putting into the smart stride shouldn’t be drawing anything more than 2 amps at a time. To lower the total cost when buying buck-boost regulators, we should find different converters based on minimal need for each component. For example, we don’t need to buy a twenty-dollar 12V, 2A regulator for some small IR sensor that needs 5V 5mA. We could find something way less costly like a LT1302 that costs in the range of $7-$10.
Unfortunately the buck-boost has other downsides compared to the other two regulators like size and cost but it serves the need of supplying power within a range that the other two converters can’t fulfill. The buck-boost regulator will be our regulator going forward. Below this section is a table that we made to help us
Criteria | Buck Regulator | Boost Regulator | Buck-Boost Regulator
Average Cost | 4$ | 8$ | 20$
Durability | High | High | Moderate to High
Operating Range | 3V to 20V | 5V to 30V | 3V to 30V
Size | Compact | Compact to Moderate | Moderate to Larger
Lifespan | 5 to 10 years | 5 to 10 years | 3 to 7 years
Maintenance | Minimal | Minimal | Minimal to Moderate

find the most suitable choice buck-boost regulator for the Kinect and other similar power-drawing components:

Table 3.3: Part Comparison of Buck-Boost Regulators
Manufacturer | Model | Price | Size | Max Current Output | Supplier
Onsemi | LM2596DS ADJR4G | $2.41 | 7 X 6 X 4.5 (mm) | 3A | Digikey
National Semiconductor | LM2577SX -12/NOPB | $3.27 | 10.16 X 4.57 X 13.97 (mm) | 3 A | Digikey
HiLetgo | XL6019 | $8.99 (3-pack) | 50 X 28 X 13 (mm) | 5 A | Amazon

Out of the options above, the most suitable choice is the LM2596 made by Onsemi. It is the cheapest out of all of the options per unit and when we buy it in bulk, it will be even cheaper. It makes sense to go with the LM2596. The input voltage range is from 4.5 V to 40 V. A wide input range is nice even though we only needed a range from 22V to 28V. Just in case if we decide to hook another battery up in series to supply more power, we have that extra room to go to 40 V if we wanted. Another reason we decided to go with the LM2596 is because of the sizing. This model had the smallest size out of the other models. An overall goal our team has kept in mind during the research phase is to find appropriate sized components, that way they fit on the wheelchair to where it doesn’t add too much weight, or get in the way when the user operates the chair. For a project like this, the voltage regulator needs to be compact to avoid overcrowding the chair’s base, which houses all of the electrical components. That’s why the LM2596 is a good fit.

While the LM2596 is going to be used with the Kinect, its wide varying input voltage range as well as adjustable output option could be used for other components. If we decide to buy in bulk with this type, it will probably be cheaper to do this than to buy many different single unit regulators from different suppliers. This will be a good thing to keep in mind for when we figure out our total parts list and see how much power needs to be supplied to each separate component. We predict that we won’t need more than 10 LM2596 regulators for the total project. Four to five will be needed for all of the components while the five to six of them will be used as backups just in case if something happens to the others.

## Voltage Regulation When it Comes to the Motors

When it comes to figuring out how we are going to place the voltage regulators in the chair, we have to keep in mind the feedback the motor produces. The motor doesn’t produce feedback the whole time while the chair is running but it does produce it quite a bit. Whenever the wheelchair slows down and changes direction is when the motors produce a different voltage than from the norm. These backed voltage spikes can cause our components to get fried. On top of the components possibly getting fried, the motor feedback can cause noise that could possibly interfere with our sensors and the controller. Also, this noise could cause the microcontroller to reset.
In order to fix this issue we will need to place a few more components and have a few more steps for safer measures. The first thing is to hook up a flyback diode in between the motor and the already built-in motor driver. The diode is placed in parallel with the motor terminals in reverse polarity. The motor driver already acts like a regulator making sure the voltage doesn’t fluctuate too much. Without the driver, the motor would probably stop working really quickly. Even with the driver, there is still a decent amount of noise being supplied to the motor when it surges. When the switch (MOSFET, transistor, etc) that is built in to the motor turns off, the collapsing magnetic field caused from the motor action causes the voltage to flip polarity which causes the diode to be forward biased which will cause it to absorb and dissipate the energy in a way to where it won’t cause harm to anything.
One more thing we are doing to take extra precaution is placing a capacitor in three different locations to further make sure the motor surges are minimal on the rest of the chair and its components. The first location we are going to place a capacitor is between the motor driver and the battery connection for each of the motors. The second location will be across the voltage regulator input at each device connection to make sure the regulators can handle sharp current more smoothly. The third location we will place a capacitor is across the regulator output so that it keeps the voltage as stable as possible across all the components. In order to find the capacitance needed for all of our capacitors for each of the three-places. The calculations for how we got our capacitances for each of the three areas can be found in the images section under the image “----”

### 3.2.2 Power Supply - Batteries

While doing research for the type of batteries that are going to be used to power the wheelchair and its autonomous capabilities, we got to keep in mind that the batteries must be able to fit into the existing wheelchair base that has been provided and it must meet the user manual specifications made by the MERIT company as well as the requirement specifications laid out in section 1.4 of this report. Most electric wheelchairs have a dual battery system with most of these batteries laid out in parallel. According to the MERIT MP3R user manual, the wheelchair previously had two 12V batteries laid out in series providing an amperage of around 44 amp hour.
When looking into what is needed when researching batteries and what type we are going to use, it is definite that for this project, we need the two batteries to be 12 V. For the dimensions of the batteries, they need to be at or below the dimensions of the battery compartments located in the base of the wheelchair. In The MERIT MP3R user manual, it states that the batteries it takes are group 22. Group 22 refers to a Battery Council International (BCI) group size. Group 22 NF dimensions are 9.5” L X 5.5” W X 8.9375” H. The smaller the BCI number, the smaller the dimensions of the batteries. The desired battery dimensions for this project when conducting research will be anything ranging from group 22 or lower.
It is important to note that when looking for suitable batteries, they must be able to handle a decent load. The load for this project will be the two motors, kinect V2 sensor, and main control unit. The motors will be the biggest drawers of power. Looking up the motors for the MERIT wheelchair, it was found that continuous use of the wheelchair will draw about 10 A from each motor which will be around a total of 20 A in total. The controller barely draws any power from the batteries unlike the motors. It can be assumed that max amps drawn per hour from a controller can be under 1 amp. To be on the safe side, 2 amps will be added to the total for the controller in the search for finding proper batteries. Lastly, these batteries will need to supply a load for the kinect sensor. According to an article, the V2 draws about 1.17 A on average and it peaks at 1.57 A. To be on the safe side, we will add 1.5 A for the V2 on average. Another 2 amp hour will be added to the total load calculations just in case. This is the last of our predicted load calculations.
Total load that is projected between the motors, controller, kinect v2, and any other additional add-ons is expected to draw 25.5 Amps an hour. When thinking about cost and how long the wheelchair should last considering how much the load is predicted to draw every hour, it would be nice to be able to run the chair for at least an hour and a half. In order to figure out what type of battery output is needed to supply the load for at least 1.5 hours, this equation is used: Minimum battery output needed = (Desired Run time (hours)) * (predicted load draw in an hour (amps)). Minimum battery output = (1.5)* (25.5 A) = 38.25 amp-hours. It is ok if a battery below this amp hour threshold is chosen. When choosing, we should aim for a minimum of 35 amp-hour or better. It is imperative that when researching for the proper batteries, the specs of the batteries need to be 12 V and have a minimum amperage of 38.25 amp-hour.

## Sealed Lead-Acid Batteries (SLA)

The sealed lead acid battery has been around the battery industry for a long time . In fact, this was the first rechargeable battery invented for commercial use. A good thing about the lead acid battery is that it is one of the more preferred batteries because of its durability and cost-per-watt. According to Battery University, there are “few other batteries that deliver bulk power as cheaply as lead acid.” A downside of lead acid is that it is very heavy. From the MERIT user manual, A group 22 NF battery is about 31 pounds. Having two lead acid batteries brings the load for the batteries alone to 62 pounds which is already a lot of weight for the wheelchair to support. Another downside of this type of battery is their charging capabilities. These batteries are not fast charging by any means. A typical full charge takes 14-16 hours, which isn't the most appealing selling point for consumers of the SmartStride. Even though the Sealed lead-acid battery has its cons, it has a lot of positives that would make it a good fit for the wheelchair.

## Gel Cell Batteries

Gelled lead acid batteries date back to the 1950s. There is this jelly like substance within the battery that is made by mixing sulfuric acid with a silica-gelling agent. The gelled material within the battery gives it a higher tolerance to vibrations than most batteries. This is a good thing to keep in mind for the wheelchair. The chair will definitely be used on uneven surfaces as well as go over cracks and mini objects that will cause the interior of the wheelchair to be disturbed. The gel-like material will help keep the battery more durable. Another thing to keep in mind is the gel cell has a higher tolerance to heat than a lot of other batteries. The wheelchair will want to be used outside where the conditions can get hot. This is a good thing to keep in mind. Some limitations of this battery is their sensitivity to overcharging and the manufacturing costs for these batteries are more expensive than Sealed-Lead Acid.

## Lithium-Ion Batteries

These types of batteries are pretty new. In 1991, Sony commercialized the first Li ion. The make up of these batteries are very promising and these batteries are the most popular on the market. They have a high energy density and are very light weight. These types of batteries are very ideal to put into the wheelchair. They have no charge memory meaning they do not need exercising to keep it in good shape. Their lifespan is way much more than the SLA and gel cell. A con with these batteries is their costs. They are way much more expensive than both the SLA and gel cell.

Table 3.4: Tech Comparison of Batteries

Out of the three batteries mentioned, we decided to go ahead and obtain two sealed lead-acid batteries for the SmartStride. Even though there are some downsides to this type of battery, there are several significant advantages that come with choosing the SLA. The main reason this type of battery was chosen

Criteria | Sealed Lead Acid | Gel Cell | Lithium Ion
Cost | $100 - $250+ | $120 - $300+ | $300 - $800
Lifespan | 2-4 years | 4-6 years | 8-15+years
Durability | Least Durable:Sensitiv e t over discharge, heat, and vibration. | Intermediate. Handles deep discharge better than SLA and resists heat better. | Most Durable. Longest cycle life, strong resistance to physical wear.
Operating Temp Range | -15 to 50 degrees celsius. | -20 to 50 degrees celsius | -20 to 60 degrees celsius.
Size and Weight | Group 22 NF: 38.6 pounds | Group 22 NF:37 pounds | Group 22 NF: 10.62 - 15.5 pounds (depending on type)
Safety | Can cause gassing or swelling if overcharged. | Intermediate -more sensitive to overvoltage. | Safest out of all three. Protected by battery management system.
Maintenance | Make sure to use proper voltage and avoid overcharge or deep discharge. | Use a precise charger. More sensitive to overvoltage. | Simple: don’t have to worry about overcharging because BMS handles protection.

was because of the costs. It is the cheapest battery out of the three, ranging from $100 to over $250 for the largest size being considered. Despite being one of the cheapest to manufacture, it still delivers good quality. It has a decent battery life and has a decent operating temperature range so the user can take it out in warmer clients if they would like to.
The Lithium Ion battery would have been the first choice between the three types researched but it unfortunately goes through a good chunk of the budget set in place already. Choosing SLA batteries keeps the budget on track. The wheelchair base used as the foundation for our project was originally equipped with sealed lead acid batteries. Since this type of battery previously powered the chair reliably, continuing with the same battery type is a practical choice.
Table 3.5: Part Comparison of Batteries

The Mighty Max 2-pack deal seems to be the best option out of the three. It comes in a 2-pack bundle that is relatively cheap putting the individual cost of each battery at $74.95. This is a little over $15 cheaper than buying the next lowest cost battery out of the options above. We also took our familiarity with the supplier as an option to look into when making this decision. Both Battery Clerk and Batteries Plus are reputable businesses but no one in our group has dealt with them before so that is another reason for why we went with the Mighty Max batteries.

Manufacturer | Model | Price | Size | Battery Capacity | Supplier
Mighty Max | ML35-12 | $148.99 (2-pack ) | 7.76”L X 5.12” W X 6.02” H | 35 ah | Amazon https://a.co/d/esJ kFh4 (https://a.co/d/esJkFh4)
Duracell | SLI22NF | $109.99 (each) | 22 NF 29 pounds | 35 Ah | Batteries Plus
AJC | EB1255 ONB | $90.19 (each) | 22 NF | 35 Ah | Battery Clerk https://batteryclerk.com/products/excel-eb12550n b-group-22nf-12 v-35ah-sealed-le ad-acid-replace ment-battery?ut m_source=chatg pt.com (https://batteryclerk.com/products/excel-eb12550nb-group-22nf-12v-35ah-sealed-lead-acid-replacement-battery)

It really doesn’t matter too much about the selection of the battery as long as something has the proper specs we are looking for. The specifications we were looking for were the right voltage, size and reasonable range of amp hour. The decision making for choosing a proper battery has proven to be very straightforward in this project as compared to most components. The reasoning is because each of these batteries we were researching were pretty much the same besides the cost. Mighty Max is a very good brand and also these batteries are specifically made for wheelchairs even though they can be used for a broad array of things.

### 3.2.3 Battery Level Indicator

While first testing our initially given wheelchair without modifications, we noticed that the battery indicator was not reading proper measurements from the batteries. One of the very first tests of the operation of the wheelchair, we noticed that with one of two of our batteries not charged, the indicator still read that both batteries were full. When designing the prototype, we would like to take out the battery gauge that's on the remote and replace it with a simple design concept for a battery level indicator. Below are some different types of battery level indicators we are thinking about implementing:

## LM3915 Battery Voltage Level Indicator

This first type of battery level indicator is an integrated circuit. It takes the IC (LM3915) which drives a simple 10 LED display to show the voltage level of an input signal. Each LED represents a 3 dB increase or decrease. What is nice is we can use this type of indicator for charging our wheelchair as well. Below is a picture of the schematic for this IC:

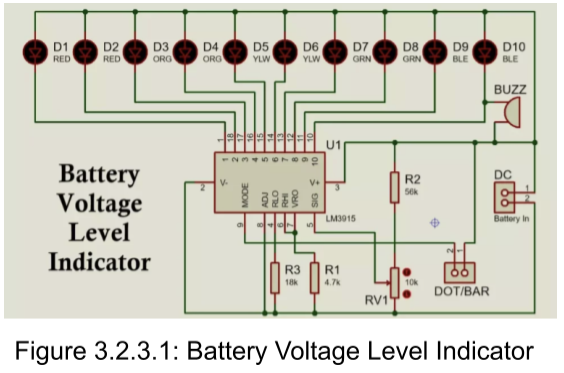
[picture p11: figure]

One side of the LM 3915 has the 10-pinouts strictly for each of the LEDs. The left side of it facing downwards in the picture has various usages for its pinout. Pin 5 is the signal input where the voltage will come through. It has a 10 KΩ potentiometer hooked up with a 56 KΩ resistor. Pins 4 and 6 on the picture of the schematic are the reference voltage pins. These pins are hooked up to the maximum and minimum voltage levels the IC will detect which is set by the external resistors. Pin 7 is used to control the brightness of the LEDs. Pin 7 is hooked up to pin 6 as well. Pin 8 is hooked up directly to the battery input. This pin will be part of the LED connections. For this pin, as the voltage increases more, more LEDs will light up. Pin 9 is the mode selection pin. This pin will allow you to switch between two different modes to show the LED display. One mode will be dot mode; this mode will show only one LED at a time. The other mode is the “bar mode” which will show multiple LEDs light up to the proper charge that the batteries are currently at. Pins 2 and 3 (located on top and bottom of the IC) are the V- and V+ inputs that are hooked up to the battery terminals. If we do decide to go forward with this design, we can either make another PCB just for this indicator or we can make it part of our main PCB that we are designing for the control unit.
Components
- LM3915 IC
- 10 LEDs
- Capacitor (optional)
- Voltage Input
- Resistors: 4.7kΩ, 18kΩ, 56kΩ and potentiometer that ranges 10kΩ.

## 16x2 LCD Hooked Up to Raspberry Pi Voltage Indicator

This type of voltage indicator may be the way to go since we can directly hook it up to the Raspberry Pi and implement it on the main PCB board design for the project.

Components
- 4 male pins
- Two pin female header
- 16x2 LCD with I2C adapter.
- Mini Breadboard (optional for testing)
- Raspberry pi 5

- Two same value resistors (10kΩ) - the smaller the value, the lesser the wasted power.
- MCP3008 - 8-channel Analog to Digital Converter

The Pi 5 does not have analog inputs, so we would need an ADC like the MCP3008. For the pinout, refer to the table below:

Table 3.6: Raspberry Pi to ADC(MCP3008) Pinout
MCP3008 Pin | Pi GPIO Pin (BCM) | Role
VDD | 3.3V | Function
VREF | 3.3V | Reference
AGND | GND | Analog Ground
DGND | GND | Digital Ground
CLK | GPIO18 | SPI Clock
DOUT | GPIO23 | SPI MISO
DIN | GPIO24 | SPI MOSI
CS/SHDN | GPIO25 | SPI Chip Select

Table 3.7: I2C LCD Wiring
LCD pin | Pi Pin | Description
VCC | 5V | output
GND | GND | Ground
SDA | GPIO2 (pin3) | I2C Data
SCL | GPIO3 (pin 5) | I2C Clock

The general wiring of the whole entire circuit is essentially a voltage-divider. The bottom of the divider will be ground. The middle tap will go to the MCP3008 (directly connected to the pi which is then connected to the LCD display) and the top of the divider to the 10kΩ. The two resistors in series mark the different parts of the divider circuit. Overall, for this design, it looks like since it is compatible with the pi which we are already using for our project, this would be the best bet for the type of voltage indicator to use.

## LM324 Battery Indicator

This type of circuit uses two quad Op-amps (LM324). Each of these two components has four outputs and 8 total inputs for the four actual op-amps which makes sense. You have an inverting and non-inverting input for each. Each of the four op-amps is used as a comparator in this circuit. There are a total of 12 resistors in this circuit. The main function of Resistors R1 through R6 Resistors are meant to prevent damage to the LEDs and maintain LED brightness consistency. R7 through R12 divide the 24V total power supply into decreasing reference voltages and feed those into the non-inverting inputs of each op-amp. Doing this will create thresholds at different thresholds. The op-amps will turn on at different voltage levels activating the LEDs that are hooked up to them. For example, the top op-amp can be set to turn on at the 24.5 to 25V voltage mark which indicates a full charge, that op-amp can be connected to the two green LEDs(one darker than the other) indicating a full charge.

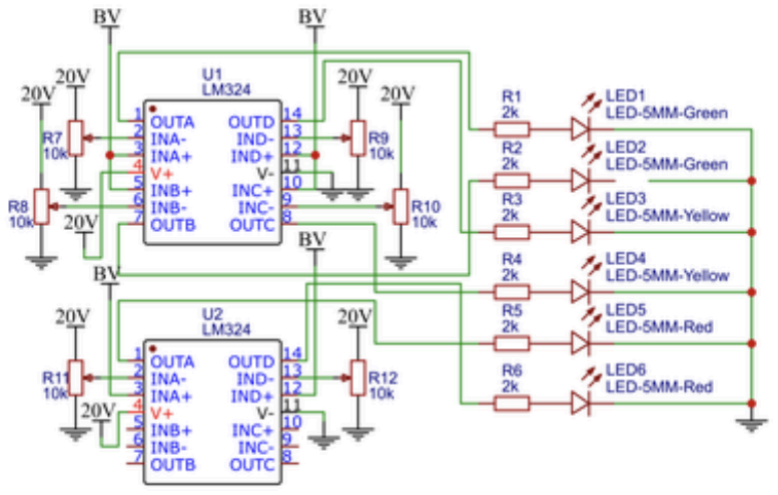
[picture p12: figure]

Figure 3.2.3.2: LM324 Battery Indicator

Components
- 12 Resistors: 6-2kΩ, 6-10kΩ,
- 2 LM324’s
- 6-5mm LED: 2-green, 2-yellow, 2-red
In order to implement a design like this, we need to find a good voltage range to set for our op-amps to turn on or off which will control the LEDs. So, since we have two 12V batteries in series, we can expect our battery range from full charge to total discharge is something like 25 V to 21.6 V. It would be Ideal for each LED being a + or - 20% increment of the total battery life. Looking at the table below:

Table 3.8: Ideal LED Fluctuating Voltage Range
LED# | Lights Up Above | % Charge
LED1 | > 25V | 100%
LED2 | >24.5V | 80%
LED3 | > 24V | 60%
LED4 | > 23.5V | 40%
LED5 | > 23V | 20%
LED6 | > 22.5 V | 0%

The highest reference voltage goes to the comparator tied to LED1. Each comparator will use a +/- 0.5 V differential when reading the battery status. When the battery voltage is below a certain threshold, that comparator will stay off and that LED will not come on. Overall, this type of design would work very well. The only thing that we do not like about this design is the amount of components in it. It has a total of 20 components.

Table 3.9: Tech Comparison of Battery Voltage indicator
Feature | LM 3915 LED Bar Graph | 16x2 LCD +Raspberry Pi + MCP3008 | LM324 Comparator
Display Type | 10 segment LED bar graph | 16x2 LCD Screen | 6 LEDs
Voltage Threshold | Logarithmic scale (3 dB steps) | Programmable | Fixed (0.5V steps)
Component Count | 15 | 3 | 20
Estimated Power Consumption | 0.48 to 0.96 W | 5 W | 0.24 to 0.48 W
Cost | $15-17 | $25-40 | $13-15
Complexity | Medium: hooking up 10 LEDs indirectly to one op-amp. | Little: hooking up 16x2 LCD to MCP3008 then to pi and coding | High: Working with 8 op-amps technically. They are known to cause issues

Based on the table above, we made our decision to go with the LM3915 LED bar graph. One of the biggest reasons we decided to go with this design was mainly due to power consumption and cost. When we picked our batteries out, we specifically set aside about 1.5 A more of current draw from them for unexpected loads we haven't thought about yet. The battery indicator was something we initially didn’t think of implementing into our project, so when we decided to implement this, we had to keep in mind the 1.5 A. Cost was the second biggest reason because it is one of our biggest priorities to stay within our planned budget as shown in chapter 10.
We really wanted to go with the 16x2 LCD indicator with how easy it is to set up and there aren’t many parts. The main reason we decided not to go with this and go with the LM3915 is because its power consumption was way too high. 5 W is what it will draw around 210 mA at 24 V. The power draw for the LCD 16x2 is still well within the 1.5 A load that we have left to work with but we would rather go with something that will draw significantly less just in case if we have to add more onto the general load later. By the way, the LM3915 draws 20 to 40 mA.The only thing we do not like about the LM3915 voltage indicator design is the amount of parts. We could lower our LED count from like 10 to 3 but it would be better to have more LEDs so we can be more precise with the battery status. The design is time consuming to put together on a PCB because of the component count but this was to be expected and is not a big obstacle for us.

## 3.3 Processing Unit Research

We need a processing unit that will interpret the sensor and run the self-driving algorithm. As such we need to pick a processing unit that is fast enough since this is a real time system and needs to have low processing times. Also, since we are considering sensors with high data throughput requirements, we need to spec a unit that has these requirements in mind if we want to be able to use these sensors. We also need to make sure it has the proper pinouts we need to connect to said sensors and also preferably easy to program for the task. Most processing units we will look at are called Single Board Computers (SBC) since our project requires lots of processing power.

### 3.3.1 Raspberry Pi

The Raspberry Pi family of boards are very popular for many projects. As such it has much documentation of its use and also is quite powerful compared to similar SBCs of its class. However due to its popularity, its demand is quite high and as such pricing can be high. It also is a general purpose SBC so it doesn't excel in our specific use case. These problems can be overcome by savvy purchasing and a sufficiently powerful board to forgo any inefficiencies of being a general purpose SBC

Raspberry Pi 3 Model B+
This SBC is probably the most recognized and popular as it’s been out the longest. It sports 4 USB 2.0 ports, 1GB of LPDDR2 RAM, and a 1.4GH Quad Processor. At the time it wasn’t powerful, but it had very low power consumption, easily accessible GPIO pins, and a very low price point. Normally for our project this would fit the bill as GPIO based sensors don’t require that much processing power. In our case however, we need a 5Gbps USB port and OpenCL acceleration that the Pi 3 is not capable of. As such this SBC is not enough.

Raspberry Pi 4 Model B
The Pi 3 is quite similar to the Pi 4. The main difference is the larger RAM size (a variety of RAM sizes from 1GB to 8GBs) and faster ram. Much faster processors that consume less power. The main draw from the Pi 3 is 2 USB 3.0 ports in place of 2 USB 2.0 Ports. This fulfills the requirement of a 5Gbps data connection for the Kinect v2 we are planning to use. It does have a slight problem however, it doesn't have GPU acceleration for OpenCl applications. We need this if we want to properly process the Kinect v2’s data. We can offload it to the CPU for processing, but that increases power draw and can be problematic for our real time component of this system.

Raspberry Pi 5
The most powerful Raspberry Pi to date, with many features over the Pi4 but has similar specs. The main difference is OpenCl acceleration, which allows for the cpu to be freed for our programs when accelerating processing the Kinect’s data. It also has a cooling fan that we can put on it to have stable operation. Since this device may be outside in hot weather, it is helpful to have a cooling system built in to keep the system stable.

It does consume more power which may be a problem for our use case, and it runs at a weird 5V 5 Amp power draw to get full performance which is a nonstandard USB PD profile. However we can still power it via the GPIO pins or run it at the lower 5V 3 Amp profile (which reduces the usb port’s power management and other nonessential systems) if we can’t find a way to power at the 5V at 5 Amps.

It also has the same pinout and formfactor of the others whilst being the most popular amongst hobbyists. This means many users have documented projects using this model. It also means it is the most supported of the libraries we need to run our sensors.

Table 3.10: Tech Comparison of Processor

Criteria

Raspberry Pi 3
Model B+

Raspberry Pi 4
Model B | Raspberry Pi 5
Processor | 1.4GHz quad-core ARM Cortex-A53 | 1.8GHz quad-core ARM Cortex-A72 | 2.4GHz quad-core ARM Cortex-A76
RAM | 1GB LPDDR2 | 1GB, 2GB, 4GB, or 8GB LPDDR4 | 4GB, 8GB, 16GB LPDDR4X
USB Ports | 4x USB 2.0 | 2x USB 3.0, 2x USB 2.0 | 2x USB 3.0, 2x USB 2.0
Video Output | 1x Full-size HDMI | 2x micro-HDMI | 2x micro-HDMI
Power Consumption | ~3.5W (idle), ~5.1W (load) | ~3.4W (idle), ~7.6W (load) | ~4.0W (idle), ~9.5W (load)
Bluetooth | Yes | Yes | Yes
UART | Yes | Yes | Yes

PWM | No | Yes | Yes
SPI | Yes | Yes | Yes
Special Features | - | - | PCIe 2.0 interface, Active cooling header
OpenCl Acceleration | No | No (Possible with CPU) | Yes
Price | ~40$ | ~70$ | ~90$ + (7.99 for Active Cooler)

Some more notes as all the Pi’s share some of these limitations and also some of these benefits.

The Raspberry Pi’s all have GPIO pins that have SPI, I2C, and UART functionality. So we can lean on those communication protocols for sensors and parts that need this connection. The GPIO pins are also limited to digital outputs only, and have only a few mAmps that it can push out. This is limiting as we may not be able to power a sensor purely on a few pins as that adds complexity. Also without Analog outputs, it means we will need to integrate Digital to Analog Converters to allow this functionality.

### 3.3.2 Nvidia Jetson

The Nvidia Jetson is a very similar competitor to the Raspberry Pi, however its main claim to fame is its very powerful GPU that is integrated. As we require a very powerful GPU for our Kinectv2, it makes sense to look into these Single Board Computers that have solid GPU performance whilst also being low powered. On the surface this seems to be an easy choice to forgo Pi’s or other Single Board Computers. However, there are some major considerations to be made. Mainly cost and niche appeal means that it is difficult to acquire and also difficult to program for with much less user documented projects. Even the cheaper models are out of production so it is difficult to find on the used market. This is compounded by its niche appeal so it is often not found on the used market. Since we want this project to be made with easily found parts and cheaply, we need to consider the pros of using this SBC. We also need to remember that most of these systems need a development board that may not be a part of the product, which is highly unusual for

Jetson Nano
The Jetson Nano is the first and oldest of the Jetson line. It is also the cheapest but prices fluctuate since it is discontinued. Despite that it is a very capable SBC, with 4 USB 3.0 ports and a 128-core Maxwell GPU. This makes the GPU performance in even this older module much higher than any other SBC mentioned in this paper. It also has very developed video encoding and decoding performance so it is capable of many video streams if we elected to use RGB camera sensor arrays. It has 4 Gigabytes of RAM, which is modest for its power and is quite fast for SBC of its weight class.

Jetson Orion Nano 4GB
This model is a much more modern version of the Original Nano, with a lot more GPU compute and a marginal amount of CPU compute. It has the same amount of RAM as the previous Nano, which was fairly generous initially so it's not too strange here. The main benefit of the Orion over the original Nano is that it has an Ampere architecture as its GPU. These cores power the 3000 series GPUs from Nvidia, and are very powerful for AI workloads. The AI special Tensor cores are the real claim to fame, meaning we can have AI workloads running in tandem to other GPU workloads since AI can gobble up a lot of GPU compute without guard rails. Ampere also brings more advanced video transcoding support.

To note too is that we get 2 more ARM cores compared to the original Nano, which are faster, meaning that the CPU power is also quite respectable. However, we only found modules listed online, which means we would need to source a dev kit if we wanted to utilize this powerful computer module.

Jetson Orion Nano 8GB
Even though this SBC is named the same as the 4GB module, it is doubled in both GPU and RAM as opposed to just RAM. This means that anything the Orion 4GB can do, this 8GB model does better. This SBC also has some consideration where it can consume much more power if enabled, which means that we can get much higher clock speeds from the SBC. This in turn means that we can enable a “Super” Mode that unlocks the power limit. This leads to much higher performance overall at the cost of power consumption. This is a blessing for embedded systems with Power Supplies connected to the grid as they don’t need to consider power consumption as greatly. However for our battery focused project this Super Mode would be much more limited for our uses as we don’t want to bring excessive power consumption.

Table 3.11: Tech Comparison of Nvidia Jetson Type
Feature | | Jetson Orin Nano 4GB | Jetson Orin Nano 8GB (Super Dev Kit)
MSRP | ~$150 (Discontinued, market price) | ~$159 (Module only) | $249 (Developer Kit)
GPU Performance | 0.472 TFLOPS (FP16) | 20 TOPS (INT8, sparse) | 40 TOPS (INT8, sparse)

Jetson Nano
(Original)

GPU | 128-core Maxwell | 512-core Ampere, 16 Tensor Cores | 1024-core Ampere, 32 Tensor Cores
CPU | Quad-core ARM A57 @ 1.43 GHz | 6-core Arm Cortex-A78AE | 6-core Arm Cortex-A78AE
Memory | 4 GB 64-bit LPDDR4 | 4 GB 64-bit LPDDR5 | 8 GB 128-bit LPDDR5
Memory Bandwidth | 25.6 GB/s | 34 GB/s | 68 GB/s
Power Modes | 5W / 10W | 7W / 10W | 7W / 15W (25W Super Mode)

The Jetson line of Single Board Computers are very compelling, due to their high performance ceiling and GPU compute. Which brings many benefits to our systems and sensors. However it has a much more aggressive price that must be weighed with our price to performance targets.
Okay, here's a rewritten and expanded version of all the sections regarding potential computing platforms, incorporating more detail and aiming for better flow, based on the provided context.

### 3.3.3 x86 Computers: A Familiar Foundation with Significant

Drawbacks

The x86 architecture consistently emerges as a potential consideration when designing the control unit for our wheelchair project. Its primary appeal lies in its widespread adoption and inherent software compatibility. Virtually all existing software is designed to run on x86 systems, a major advantage simplifying development and integration. Furthermore, the architecture's longevity means it's readily available in legacy hardware, though this often comes with a trade-off in efficiency. However, a key challenge is the inherent power inefficiency of x86 systems. This presents a significant hurdle for a battery-powered wheelchair application, making them generally unsuitable without careful consideration and mitigation strategies. Despite this, we will analyze them as potential options, reserving the possibility of integration should their benefits outweigh the power consumption drawbacks.

LattePanda 3 Delta

The LattePanda 3 Delta stands out as a unique offering within the x86 landscape. This Single Board Computer (SBC) distinguishes itself with its Intel N5105 processor and a robust 2.5 Gigabit Ethernet connection. While x86 systems aren't typically known for extensive GPIO capabilities, the LattePanda 3

Delta bucks this trend, providing a comprehensive suite of GPIO pins alongside USB and audio connectivity. It also boasts NVMe SSD support for fast storage and provides expansion slots for 4G/5G cellular connectivity. A significant benefit is the ability to program it using familiar tools and environments, mirroring standard computer development workflows. Specifically, the ability to run Windows environments is valuable for leveraging existing Kinect v2 integrations and providing a comfortable development experience for a portion of our team. However, the core issue remains: power consumption. As with all x86 systems, the LattePanda 3 Delta suffers from significant inefficiencies, posing a serious challenge to battery life within the wheelchair application. Furthermore, the integrated Intel CPU delivers a comparatively slow GPU, limiting its suitability for computationally intensive tasks like real-time image processing.

x86 Mini Office PC

One team member possesses a compact x86 system—a Dell Optiplex 9020M. This system is equipped with 8GB of DDR3 RAM and an Intel Core i7-4785T processor, a quad-core, eight-thread CPU with a Thermal Design Power (TDP) of 35 Watts. While offering reasonable performance, the 35-Watt TDP immediately raises concerns about power efficiency for our application. The pre-built nature of the system offers a convenient starting point, but customization options are limited. The older DDR3 RAM and the relatively modest GPU capabilities of the integrated Intel graphics further restrict its potential.

Desktop DIY System

Constructing a custom desktop system presents an attractive prospect, potentially delivering the highest performance for the lowest cost, particularly given the availability of spare parts among our team members. However, this approach introduces substantial complexity and significant power consumption challenges, extending the concerns we've already noted with existing x86 systems. A key hurdle is creating a suitable power supply capable of providing the multitude of voltages required by a desktop PC. This would likely necessitate a substantial power supply PCB and potentially require DC-to-AC conversion, leading to significant power loss and the need for larger, more powerful batteries. Implementing a bespoke system of this nature presents considerable engineering challenges and would likely be a complex and time-consuming endeavor.

Server/Cloud Processing

Leveraging server or cloud processing represents a fundamentally different approach, moving computation offboard the wheelchair itself. This offers the advantage of functionally unlimited processing power, and the potential for cost savings through a “pay-per-compute” model. This is particularly appealing for computationally intensive tasks that don't require immediate, real-time responses. However, the primary drawback is increased latency due to the need to transmit data to and from a remote server. This latency could be detrimental to the responsiveness of our self-driving system. While cloud computing is utilized in various self-driving applications, a reliable and fast cellular connection would be essential for mitigating latency issues. Services like AWS VPSs could be utilized to set up a remote processing system, potentially enabling remote wheelchair control, provided sufficient bandwidth is available.

Table 3.12: Comparison of Processing Platforms for System Integration

Feature | LattePanda 3 Delta | x86 Mini Office PC | Desktop DIY System | Server/Cloud Processing
Processor | Intel Celeron N5105 | Intel Core i7-4785T | AMD Ryzen 5 2600 | Variable
Graphics (GPU) | Intel UHD Graphics (Integrated) | Intel HD Graphics 4600 (Integrated) | NVIDIA GeForce RTX 2060 (Dedicated) | None / High-End
Memory (RAM) | 8GB LPDDR4 | 8GB DDR3 | 16GB DDR4 | Variable (e.g., 0.5GB - 2GB)
Upfront Cost | ~$280 - $330 | $0 | ~$500 - $700+ | ~$0 (Free tiers available)
Power Profile | Excellent. Very low consumption. Idle: ~1.5W Load: ~15-18W | Poor. Moderate consumption. CPU TDP: 35W System Load: ~40-50W | Impractical. Extreme consumption. System Load: ~300-350W | N/A (Handled by provider)
Physical Size | Pocket-sized. (125 x 78 x 16mm) | Compact. (Small Form Factor PC) | Large. (Standard desktop tower) | N/A (Cloud-based)
Connectivity & Expandabilit y | Excellent. Wi-Fi 6, 2.5Gb Ethernet, GPIO, NVMe, 4G/5G option. | Fair. Standard ports (USB, Ethernet), limited internal expansion. | Excellent. Highly customizable with PCIe slots, multiple drive bays, and ports. | Internet connection is the only interface. Need on site computer to encode inputs

Developmen t Environment | Easy. Familiar Windows/Linux on modern hardware. Supports Kinect v2 well. | Easy. Familiar Windows/Lin ux, but on older architecture. | Easy. Familiar Windows/Linux on the most powerful hardware. | Complex. Requires remote development, managing instances, and network programming.
Key Pros | • Best balance of performance and power. • Onboard GPIO for sensors. • Modern I/O (NVMe, 2.5GbE). | • No cost to acquire. • More powerful CPU than LattePanda. • Convenient pre-built form factor. | • Highest local performance. • Unmatched for intensive tasks. • Fully customizable/u pgradable. | • Virtually infinite, scalable power. • Cost-effective "pay-per-comput e" model.
Key Cons | • Weaker CPU/GPU performance compared to desktops. | • Poor power efficiency for battery use. • Very weak integrated GPU. | • Extreme power consumption. • Complex power delivery required. • Large size and weight. | • High latency • Requires constant, fast internet. • Can become expensive with usage.

x86 Conclusion
With all these options in front of us, the Mini PC seems like the best choice. It is the cheapest of the bunch, whilst providing as many benefits of x86 we can muster. It does provide some challenges, such as its weaker GPU and higher power draw compared to the SBC. Its lack of latency with cloud services and small size make it an ideal middle ground and get us closer to the non-x86 computers listed.

### 3.3.4 Processing Unit Conclusion

Lets take the 3 choices from the last sections and compare them. We can then see which one we should choose ultimately between all of them.
Table 3.13: Comparison of Compact Computing Platforms

Feature

x86 Mini PC (Dell
9020M) | Raspberry Pi 5

Original Jetson Nano
4GB

Processor (CPU) | Intel Core i7-4785T (4-Core) | 2.4GHz Quad-core ARM Cortex-A76 | 1.43GHz Quad-core ARM A57
Graphics (GPU) | Intel HD Graphics 4600 | VideoCore VII (OpenCL) | 128-core Maxwell (CUDA)
Memory (RAM) | 8GB DDR3 | 8GB LPDDR4X | 4GB LPDDR4
Power Profile | Poor (~40-50W Load) | Excellent (~9.5W Load) | Excellent (5W / 10W Modes)
Cost & Availability | $0 (Owned) | ~$90 (Widely Available) | Discontinued (High used price)
Ecosystem | Familiar PC Environment | Vast Community & Support | Niche AI Community
Key Pros | • No upfront cost • Strong CPU | • Low cost & available • Huge ecosystem • Meets all project needs | • Strong GPU for its time • 4x USB 3.0 ports
Key Cons | • Very poor power efficiency • Extremely weak GPU | • Weaker GPU than Jetson • Nonstandard power input | • Outdated & hard to find • Slower CPU

Our Team decided to go with the Pi 5. This was due to it being the solid middle ground over all the other options. The lower power consumption, small size, and GPU acceleration makes it most ideal. Another important reason is the fact it is a highly available and popular part. This project we want to make in a way that it can be somewhat applied to other chairs and using parts that can be easily sourced, utilizing non-standard parts and depending on niche availability is against this goal. So we finally come to our chosen part, the Raspberry Pi 5.

## 3.4 Wireless Processing Unit Research

Table 3.14: Evaluation of Wireless Protocols for Embedded Systems
Technol ogy Name | Frequen cy Band | Typical Data Rate (Mbps/k bps) | Typical Range (Indoor/ Outdoor, meters) | Latency (ms) | Power Consum ption (Active/S leep) | Interfere nce Suscepti bility | Key Security Features | Network Topology
BLE | 2.4 GHz | 1-2 Mbps | 10-240m | Not | Low | Moderate | AES-128, | P2P,

| ISM | | | specified, but "fast connectio n" | (months-years battery) | (2.4 GHz band) | SSP/Sec ure Connecti ons, ECDH | Star, Mesh
UWB | 3.1-10.6 GHz | Up to 27 Mbps | Optimal: 1-50m; Max: 200m | <1 ms | Very Low (ÂµW-m W, long battery) | Very Low (wide band) | Time-hop ping spread spectrum , concealm ent | P2P
Zigbee | 2.4 GHz ISM | Up to 250 kbps | Indoor: 10-100m; Outdoor: 300m | Low (often <300ms) | Very Low (25% of Wi-Fi, years battery) | Moderate (2.4 GHz band) | AES-128, authentic ation, key manage ment | Mesh
Z-Wave | 900 MHz ISM | Up to 100 kbps | Indoor: 30m; Outdoor: 100m (extenda ble) | Low (often 300-800 ms) | Low (years battery) | Low (900 MHz band) | Advance d encryptio n (S2), authentic ation | Mesh
Proprieta ry RF | Sub-GHz , 2.4 GHz | Highly configura ble | Highly configura ble (long range possible) | Very Low (optimize d) | Very Low (years battery) | Configura ble (Sub-GH z is low) | Customiz able, low-level access | Flexible (P2P, Mesh, etc.)
Wi-Fi | 2.4 GHz, 5 GHz | Up to 1 Gbps | Optimal: 0-50m; Max: 500m | 5-100 ms (variable) | High (80-260m A active, 5-20W router) | High (2.4 GHz band, congestio n) | WPA2/3, enterpris e security | Star (AP-centri c)

### 3.4.1 Communication technologies

Multiple wireless technology standards should be compared to come up with one that meets the use case of our chair. We need a low latency, small power consumption and a decent range. We aren’t expecting to move the chair from miles away but a feasible distance for remote control is ideal. Certain wireless technologies benefit more when in large clusters or in huge nodes of multiple devices. This isn’t in line with our use case so while we may look into these technologies a bit they won’t be our main focus.

### 3.4.1.1 Ultra-WideBand

Ultra-WideBand transmits data and signals over bandwidths larger than 500MHz. Ultra wide band systems are currently utilized to determine real time location thanks to reliability and accuracy. It functions well in indoor environments with examples being industry use in medical and healthcare facilities. Real time movement tracking and time of flight information are all regular applications behind this technology. Implementing this with actual equipped electronics could be costly compared to other technologies presented.

### 3.4.1.2 Zigbee

The ZigBee network technology has its primary use in mesh networks with multiple low power devices operating and communicating together on the meshed network. It operates in the 2.4GHz ISM band and supports rates up to 250kbps. It is designed for low latency communication. Zigbee networks are also much more power efficient in comparison to other technologies like Wi-Fi. Its primary specialties are mesh networking utilizing devices as relays that can extend the networks range. While useful this doesn’t fall in line with our specific needs.

### 3.4.1.3 Z-Wave

Z-Wave is another Mesh network communication technology that focuses on low power and utilizing an incredibly low bandwidth range of below 1Ghz. This allows for less interference from other communication that may occur on more congested bands like the 2.4Ghz one. Z-Wave has uses in home IOT devices like lights and other low data rate hardware. It communicates at a pretty slow 100kbps but for its intended applications this is suitable.

### 3.4.1.4 Bluetooth Standard

The Bluetooth Standard is a widely known and adopted communication standard for consumer devices like phones and speaker bars. Bluetooth utilizes a master/slave architecture with the master communicating with up to seven slaves. The master sets the clock speed for packet exchange. The role of master and slave can change based on both devices agreeing and the function of the use case. This allows for some versatile applications of the communication technology when interfacing one device with multiple bluetooth connections. Bluetooth operates on the unlicensed 2.4GHz ISM band. This allows us to utilize these frequencies freely without needing to request authorization from anyone else.

### 3.4.1.5 Bluetooth Low Energy standard

Created with the intention of maintaining similar communication ranges and capabilities as regular bluetooth while using much less power. It operates on the 2.4GHz radio frequency. The power efficiency is met but using bursts of data transmission as well as regular intervals in low power states outside of transmission times. Devices usually need a profile, something that tells the protocol how exactly the device is operating. Most use the (GATT) Generic Attribute Profile for sending and receiving data simply. BLE is also capable of a mesh effect where multiple devices on BLE can send information to one another in almost a cascading effect of data transfer. This allows for the control of multiple devices at once easily. BLE sends data using a 2MHz spacing that allows for 40 channels of data transmission.

### 3.4.2 ESP32

The ESP32 is a 2.4ghz dual core microcontroller with Wi-Fi and Bluetooth capabilities. A main point of the board is also its FreeRTOS framework. This preemptive OS is extremely well made for multi tasking and proper task scheduling and priority control. This allows for quick interrupts that can enable speedy control transfer between autonomous driving and controlled driving. The ESP32 also boasts a large number of ADC channels at 16 counts. It also has 2-8bit DAC channels for analog output. This is essential for our joystick signals to be read. The ESP32 is also very cheap and low power draw as well with an amp of draw when bluetooth and wifi are both running while cores are processing data. A 3.0v to 3.6v requirement allows for easily replaceable or rechargeable single cell batteries. Further lending to our accessible design. Avoiding proprietary design constraints helps allow our users to repair and continue to use the wheelchair as much as possible.
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

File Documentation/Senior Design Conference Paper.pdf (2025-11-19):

# SmartStride (The Future of

Mobility: Hands-Free,

# Affordable, and Intelligent)

Matthew Itskovich, Evan Reese, Arturo Lara,

### and Adam Lilly

### Dept. of Electrical Engineering and Computer

Science, University of Central Florida, Orlando,

### Florida, 32816-2450

Abstract – SmartStride is an affordable, hands-free mobility system designed to retrofit existing electric wheelchairs with autonomous capabilities. The system integrates a Raspberry Pi 5-based control unit that processes data from a magnetometer and infrared depth sensor (Kinect V2) to enable real-time obstacle detection and navigation. Five custom PCBs support the design: three voltage regulator boards using LM2596 and AMS1117 chips, a Bluetooth communication controller, and a Pi-to-Wheelchair interface board. Together, these modules create an
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

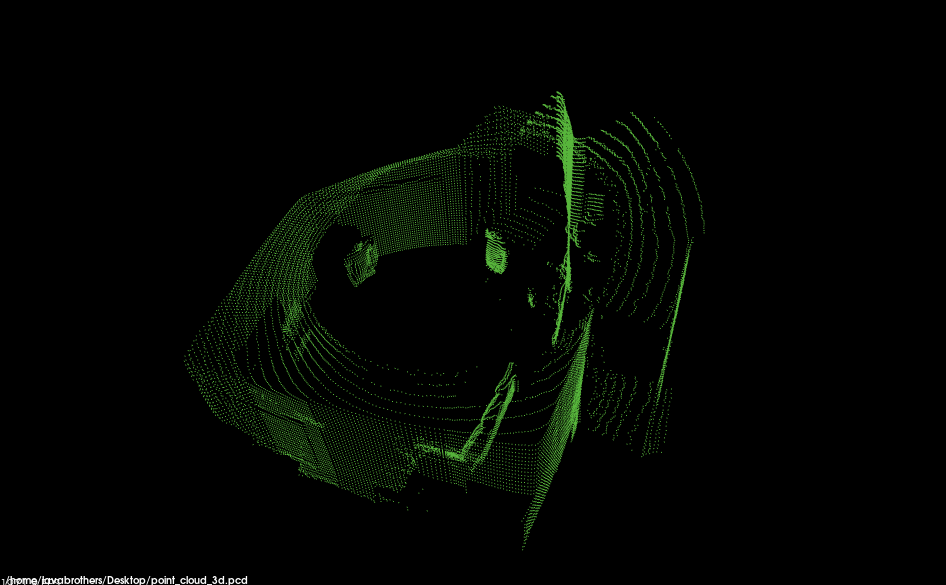
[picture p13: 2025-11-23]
Map Examples/Apartment.png

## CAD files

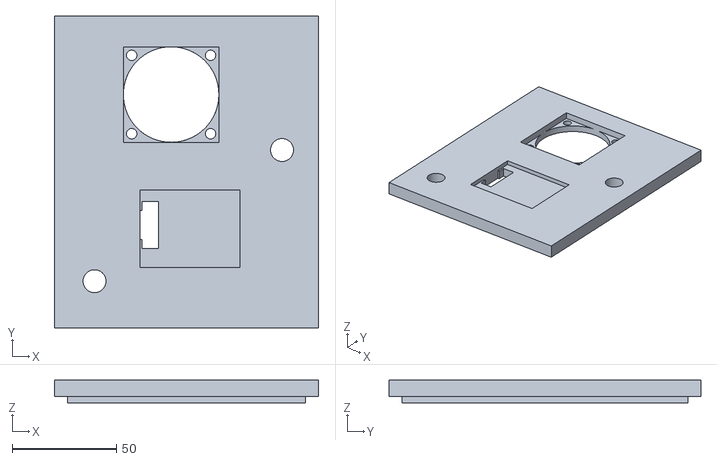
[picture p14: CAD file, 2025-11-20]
Fusion Files/STLs/Top Controller Board.stl
126.5 x 149.4 x 11.0

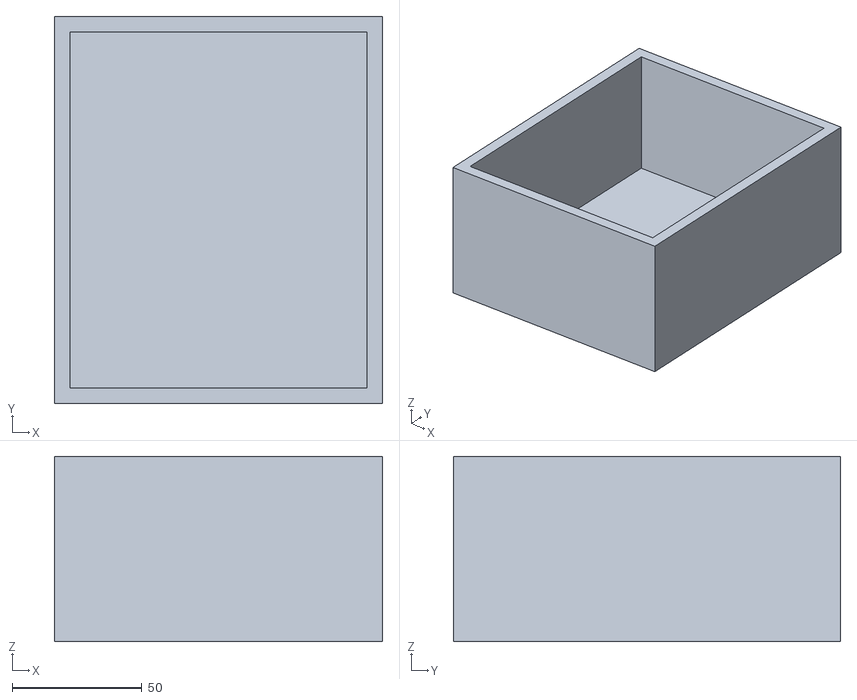
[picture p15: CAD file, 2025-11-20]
Fusion Files/STLs/Bottom Controller Box.stl
126.5 x 149.4 x 71.5

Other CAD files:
Fusion Files/Schematics/3.3V Regulator - AMS-117.f3z
Fusion Files/Schematics/5-12V Regulator.f3z
Fusion Files/Schematics/ESP32 Controller.f3z
Fusion Files/Schematics/MCP4728.f3z
Fusion Files/Schematics/Pi Mainboard.f3z

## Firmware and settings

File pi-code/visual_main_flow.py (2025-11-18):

"""
visual_main_flow.py

This module implements the main asynchronous control flow for the self-driving
wheelchair, specifically designed for operation with a Bluetooth controller
and integrated real-time visual feedback. It combines various autonomous modes
(cruise, follow, mapping) with Bluetooth command input and displays live video
feeds or status screens using OpenCV.

The system manages transitions between different operational states (MANUAL, CRUISE,
STOPPED, FOLLOW, MAPPING) and provides audio feedback for state changes. It leverages
vision for obstacle detection and person tracking, and allows for environmental mapping.
Robust initialization and reconnection logic ensures system stability.

Key Features:
- Integrates Bluetooth command input for mode selection and manual control.
- Implements autonomous cruise control with a 2-stage obstacle detection (person and general path).
- Provides autonomous person following, adjusting speed and direction to maintain distance and centering.
- Supports environmental mapping with a 360-degree scan, which temporarily shuts down vision.
- Displays real-time visual feedback via an OpenCV window, showing sensor data or status.
- Provides audio cues for mode changes.
- Includes robust initialization and cleanup procedures for all hardware and software modules.

Dependencies:
- asyncio: For managing asynchronous tasks and the event loop.
- time: For timing operations and safety timeouts.
- enum: For defining control states.
- threading: For managing the mapping stop event.
- bluetooth_module: Custom module for BLE communication with an ESP32 controller.
- wheelchair_control (wc): Custom module for controlling the wheelchair's motors via a DAC.
- person_detector (vision): Custom module for detecting persons and obstacles using a Kinect sensor.
- mapping_module (mapping): Custom module for environmental mapping.
- audio_feedback (beeper): Custom module for providing audio cues.
- cv2 (OpenCV): For image processing, visualization, and displaying video feeds.
- numpy: For numerical operations and array manipulation of image data.
"""

import asyncio
import time
from enum import Enum
import threading
from bluetooth_module import BluetoothModule
import wheelchair_control as wc
import person_detector as vision
import mapping_module as mapping
import audio_feedback as beeper
import cv2
import numpy as np

# --- Constants ---
ADC_MAX = 4095.0        # Maximum value from the ADC for joystick input scaling.
DEBUG_PRINT = True      # Enable/disable debug printouts for autonomous modes.

# --- Cruise Mode Constants ---
CRUISE_STOP_DISTANCE_MM = 1500  # Distance in mm at which to stop for general obstacles.
CRUISE_STOP_DISTANCE_FT = 4.5   # Distance in feet at which to stop if a person is detected.
CRUISE_SPEED = 0.3              # Forward movement speed in cruise mode (0.0 to 1.0).
CRUISE_TURN_TRIM = 0.03         # Small turning adjustment for drift correction in cruise mode.

# --- Follow Mode Constants ---
FOLLOW_TARGET_DISTANCE_FT = 3.5     # Desired following distance from a person in feet.
FOLLOW_DEAD_ZONE_FT = 0.3           # Tolerance zone around TARGET_DISTANCE_FT where no forward/backward movement occurs.
FOLLOW_MOVE_SPEED = 0.25            # Forward/backward movement speed in follow mode.
FOLLOW_TURN_SPEED = 0.35            # Turning speed in follow mode.
FOLLOW_TRACKING_DEAD_ZONE_PX = 30   # Pixel tolerance for person's horizontal position in the frame.
FOLLOW_TARGET_LOST_TIMEOUT_S = 3.0  # Time in seconds before declaring target lost and stopping.
FOLLOW_STOP_DISTANCE_MM = 1250      # Distance in mm at which to stop for obstacles during follow mode.
MM_TO_FEET = 0.00328084             # Conversion factor from millimeters to feet.

# --- Reconnection Constants ---
RECONNECT_DELAY_S = 2   # Delay in seconds before attempting to reconnect modules.

# --- State Management ---
class ControlState(Enum):
    """
    Defines the possible operational states of the wheelchair.
    """
    MANUAL = 1      # Manual control via Bluetooth joystick commands.
    CRUISE = 2      # Autonomous cruise control with obstacle avoidance.
    STOPPED = 3     # Wheelchair is stationary.
    FOLLOW = 4      # Autonomous person following.
    MAPPING = 5     # Environmental mapping mode.

current_state = ControlState.STOPPED    # The current operational state of the wheelchair.
last_command_time = time.time()         # Timestamp of the last received command, used for safety timeouts.
mapping_stop_event = threading.Event()  # Event flag to signal the mapping task to stop.

# --- State variables for follow mode ---
last_person_detection_time = 0.0        # Timestamp of the last successful person detection.
last_person_turn_direction = 0.0        # Last turn command issued when a person was tracked.

# --- Visualization Global ---
# This frame is updated by autonomous loops and displayed by the visual_flow_loop.
current_visual_frame = np.zeros((480, 640, 3), dtype=np.uint8) 
cv2.putText(current_visual_frame, "Initializing...", (50, 240), cv2.FONT_HERSHEY_SIMPLEX, 1, (255, 255, 255), 2) 


def handle_incoming_data(data: bytes):
    """
    Parses incoming byte data (expected to be UTF-8 encoded) from the Bluetooth
    module and updates the wheelchair's control state or manual movement.

    Args:
        data (bytes): The raw byte data received from the Bluetooth device.
    """
    global current_state, last_command_time, mapping_stop_event
    
    try:
        message = data.decode().strip()
    except UnicodeDecodeError:
        print("Received non-UTF8 data. Ignoring.")
        return
        
    last_command_time = time.time() # Update last command time for safety timeout.
    
    if message == "Cruise":
        if current_state != ControlState.CRUISE:
            print("Switching to CRUISE mode.")
            wc.stop() # Stop current movement before changing mode.
            current_state = ControlState.CRUISE
            asyncio.create_task(beeper.play_beep(3)) # Audio feedback for mode change.
    elif message == "Follow":
        if current_state != ControlState.FOLLOW:
            print("Switching to FOLLOW mode.")
            wc.stop() # Stop current movement before changing mode.
            current_state = ControlState.FOLLOW
            asyncio.create_task(beeper.play_beep(4)) # Audio feedback for mode change.
            global last_person_detection_time, last_person_turn_direction
            last_person_detection_time = 0.0 # Reset follow mode specific variables.
            last_person_turn_direction = 0.0
    elif message == "Map":
        if current_state != ControlState.MAPPING:
            print("Switching to MAPPING mode.")
            wc.stop() # Stop current movement before changing mode.
            current_state = ControlState.MAPPING
            asyncio.create_task(beeper.play_beep(5)) # Audio feedback for mode change.
            
    elif message == "STOP":
        # If currently mapping, signal the mapping task to stop gracefully.
        if current_state == ControlState.MAPPING:
            print("Requesting mapping task to stop...")
            mapping_stop_event.set()  # Signal the thread to stop.

        if current_state != ControlState.STOPPED:
            print("Switching to STOPPED mode.")
            wc.stop() # Ensure wheelchair is stopped.
            current_state = ControlState.STOPPED
            asyncio.create_task(beeper.play_beep(1)) # Audio feedback for mode change.
    else:
        # Default to MANUAL mode if an unrecognized command or joystick data is received.
        if current_state != ControlState.MANUAL:
            print("Switching to MANUAL mode.")
            current_state = ControlState.MANUAL
            asyncio.create_task(beeper.play_beep(2)) # Audio feedback for mode change.
        
        try:
            # Attempt to parse joystick values if the message format matches.
            parts = [int(p) for p in message.split(',')]
            if len(parts) == 4:
                fwd = parts[0] / ADC_MAX
                bwd = parts[1] / ADC_MAX
                left = parts[2] / ADC_MAX
                right = parts[3] / ADC_MAX
                wc.set_joystick_values(fwd, bwd, right, left)
        except (ValueError, IndexError):
            print(f"Could not parse joystick data: {message}")

async def cruise_control_loop():
    """
    Asynchronous loop for managing the wheelchair in CRUISE mode with visualization.

    This loop continuously checks for obstacles and persons using a 2-stage detection:
    1. Prioritizes stopping if a person is detected within CRUISE_STOP_DISTANCE_FT.
    2. If no person, checks for general obstacles in the center path within
       CRUISE_STOP_DISTANCE_MM.
    The wheelchair moves forward at CRUISE_SPEED with a slight CRUISE_TURN_TRIM
    for drift correction if no obstacles are detected. The `get_center_path_depth`
    function is used to provide the visual feedback for this mode.
    """
    global current_visual_frame 
    print("Cruise control loop started (2-stage check).")
    while True:
        if current_state == ControlState.CRUISE:
            
            # --- CHECK 1: PERSON DETECTION (visualize=False to avoid redundant frames) ---
            (dist_ft, _, _, _), _ = await asyncio.to_thread(vision.find_target_person, visualize=False)
            
            # --- CHECK 2: CENTER PATH OBSTACLE (visualize=True to get debug frame) ---
            (center_depth, _), debug_frame = await asyncio.to_thread(vision.get_center_path_depth, visualize=True)
            
            # Re-check state in case it changed during vision processing.
            if current_state != ControlState.CRUISE:
                continue

            # Update the global visual frame with the debug frame from center path detection.
            if debug_frame is not None:
                current_visual_frame = debug_frame 
            
            # --- DECISION LOGIC ---
            stop = False
            
            # Priority 1: Stop for any person detected within the safety distance.
            if dist_ft is not None and dist_ft < CRUISE_STOP_DISTANCE_FT:
                stop = True
                if DEBUG_PRINT: print(f"Person detected at {dist_ft:.2f}ft. Stopping.")
            
            # Priority 2: Stop for non-person obstacle in the center path within safety distance.
            elif center_depth is not None and center_depth < CRUISE_STOP_DISTANCE_MM:
                stop = True
                if DEBUG_PRINT: print(f"Obstacle on path at {center_depth/1000.0:.2f}m. Stopping.")

            # --- ACTION ---
            if stop:
                wc.stop() # Stop the wheelchair if an obstacle or person is too close.
            else:
                # If path is clear, continue cruising.
                wc.set_movement(CRUISE_SPEED, CRUISE_TURN_TRIM)
                if DEBUG_PRINT: print(f"Cruising (Trim: {CRUISE_TURN_TRIM}). Path clear.", end='\r')
        
        # Adjust sleep duration based on current state to save resources when not active.
        await asyncio.sleep(0.1 if current_state == ControlState.CRUISE else 0.5)

async def follow_person_loop():
    """
    Asynchronous loop for managing the wheelchair in FOLLOW mode with visualization.

    This loop continuously tracks a target person, adjusting the wheelchair's
    speed and turn to maintain a desired following distance and keep the person
    centered in the frame. It handles cases where the target person is lost
    and attempts to re-acquire them. The `find_target_person` function is used
    to provide the visual feedback for this mode.
    """
    global last_person_detection_time, last_person_turn_direction
    global current_visual_frame 
    print("Follow person loop started.")
    
    # Define the upper and lower bounds for the desired following distance.
    upper_bound_ft = FOLLOW_TARGET_DISTANCE_FT + FOLLOW_DEAD_ZONE_FT
    lower_bound_ft = FOLLOW_TARGET_DISTANCE_FT - FOLLOW_DEAD_ZONE_FT
    
    while True:
        if current_state == ControlState.FOLLOW:
            
            # Find the target person and get their distance, horizontal center, frame width.
            # `nearest_depth` is ignored in this flow, but `visualize=True` is used.
            (dist_ft, center_x, frame_w, _), debug_frame = await asyncio.to_thread(vision.find_target_person, visualize=True)

            # Re-check state in case it changed during vision processing.
            if current_state != ControlState.FOLLOW:
                wc.stop()
                continue

            # If no debug frame is returned (e.g., due to timeout), skip this iteration.
            if debug_frame is None:
                await asyncio.sleep(0.05 if current_state == ControlState.FOLLOW else 0.5)
                continue

            current_visual_frame = debug_frame # Update the global visual frame.
            
            status_text = ""
            status_color = (0, 0, 255) # Default to Red for 'lost' status.
            status_dist = "" # For debug print.

            if dist_ft is not None:
                last_person_detection_time = time.monotonic()
                
                # 1. --- Calculate speed based on person's distance ---
                fwd_bwd_speed = 0.0
                if dist_ft > upper_bound_ft:
                    fwd_bwd_speed = FOLLOW_MOVE_SPEED
                    status_dist = "MOVING FWD"
                elif dist_ft < lower_bound_ft:
                    fwd_bwd_speed = -FOLLOW_MOVE_SPEED # Move backward if too close.
                    status_dist = "TOO CLOSE (BWD)"
                else:
                    fwd_bwd_speed = 0.0
                    status_dist = "IN ZONE"
                
                # Calculate turning speed to keep the person centered.
                left_right_speed = 0.0
                frame_center_x = frame_w // 2
                left_bound = frame_center_x - FOLLOW_TRACKING_DEAD_ZONE_PX
                right_bound = frame_center_x + FOLLOW_TRACKING_DEAD_ZONE_PX

                if center_x < left_bound:
                    left_right_speed = FOLLOW_TURN_SPEED # Turn left.
                    status_turn = "TURN LEFT"
                elif center_x > right_bound:
                    left_right_speed = -FOLLOW_TURN_SPEED # Turn right.
                    status_turn = "TURN RIGHT"
                else:
                    left_right_speed = 0.0
                    status_turn = "CENTERED"
                
                last_person_turn_direction = left_right_speed # Store last turn for re-acquiring.
                
                # 2. --- Obstacle Override Check (REMOVED from this flow) ---
                # This flow prioritizes person following over general obstacle avoidance.

                # 3. --- Set final movement ---
                wc.set_movement(fwd_bwd_speed, left_right_speed)
                
                if DEBUG_PRINT: print(f"Follow: {dist_ft:.1f}ft ({status_dist}) | Turn: {status_turn} ✅ ", end='\r')

            else:
                # Target person not detected.
                time_since_last_seen = time.monotonic() - last_person_detection_time
                
                if last_person_detection_time == 0.0:
                    status_text = "SEARCHING..." # Initial search state.
                    if DEBUG_PRINT: print(f"Follow: SEARCHING... ❌                                 ", end='\r')
                
                elif time_since_last_seen < FOLLOW_TARGET_LOST_TIMEOUT_S:
                    # Attempt to re-acquire by continuing the last turn.
                    wc.set_movement(0.0, last_person_turn_direction)
                    status_text = "RE-ACQUIRING..."
                    status_color = (0, 255, 255) # Yellow for re-acquiring.
                    if DEBUG_PRINT: print(f"Follow: RE-ACQUIRING... ❓                              ", end='\r')
                
                else:
                    # Target lost for too long, stop the wheelchair.
                    wc.stop()
                    status_text = "TARGET LOST"
                    if DEBUG_PRINT: print(f"Follow: TARGET LOST. STOPPING. ❌                       ", end='\r')

            # Overlay status text on the visual frame.
            if status_text:
                cv2.putText(current_visual_frame, status_text, 
                            (20, 40), cv2.FONT_HERSHEY_SIMPLEX, 
                            1, status_color, 2)
        
        # Adjust sleep duration based on current state.
        await asyncio.sleep(0.05 if current_state == ControlState.FOLLOW else 0.5) 

async def mapping_loop():
    """
    Asynchronous loop for managing the wheelchair in MAPPING mode.

    This loop initiates an environmental mapping sequence. It temporarily shuts down
    the vision module to avoid conflicts during mapping, sets a dedicated
    "Mapping in Progress" screen as the visual feedback, and then re-initializes
    the vision module after mapping. The mapping process can be interrupted by
    setting the `mapping_stop_event`. After mapping (either completed or interrupted),
    the wheelchair returns to the STOPPED state.
    """
    global current_state, current_visual_frame, mapping_stop_event
    print("Mapping loop started.")
    
    # Create a static screen to display during mapping.
    mapping_screen = np.zeros((480, 640, 3), dtype=np.uint8)
    cv2.putText(mapping_screen, "Mapping in Progress...", (50, 240), cv2.FONT_HERSHEY_SIMPLEX, 1, (255, 255, 255), 2)

    while True:
        if current_state == ControlState.MAPPING:
            
            mapping_stop_event.clear() # Clear the event flag before starting a new mapping sequence.
            
            print("Temporarily shutting down vision module...")
            vision.shutdown_detector() # Disable vision to free up resources for mapping.
            
            print("Starting 360-degree mapping scan...")
            current_visual_frame = mapping_screen # Set global visual frame to the mapping screen.
            
            # Execute the mapping process in a separate thread to keep the event loop responsive.
            await asyncio.to_thread(mapping.perform_mapping, mapping_stop_event)
            
            if mapping_stop_event.is_set():
                print("Mapping scan was INTERRUPTED by user.")
            else:
                print("Mapping scan complete.")

            # Re-initialize the vision module after mapping.
            print("Re-initializing vision module...")
            if not vision.initialize_detector():
                print("FATAL: Could not re-initialize vision. Stopping.")
                asyncio.get_running_loop().stop() # Critical error, stop the entire application.
                break
            
            # Switch to STOPPED mode automatically after mapping.
            current_state = ControlState.STOPPED 
            wc.stop() # Ensure wheelchair is stopped.
        
        await asyncio.sleep(0.5) # Sleep for 0.5s when not mapping to reduce CPU usage.


async def visual_flow_loop():
    """
    Asynchronous loop responsible for displaying the appropriate video feed
    or status screen in an OpenCV window based on the current wheelchair state.

    This loop continuously updates the display, showing either live vision data
    (from cruise/follow modes) or static status screens (for manual/stopped/mapping).
    It also handles the 'q' key press to initiate graceful shutdown.
    """
    global current_visual_frame 
    window_name = "Visual Flow"
    cv2.namedWindow(window_name, cv2.WINDOW_AUTOSIZE)
    
    # Create static screens for STOPPED and MANUAL modes.
    stopped_screen = np.zeros((480, 640, 3), dtype=np.uint8)
    stopped_text = "Current State: STOPPED"
    (text_width, _), _ = cv2.getTextSize(stopped_text, cv2.FONT_HERSHEY_SIMPLEX, 1, 2)
    text_x = (640 - text_width) // 2
    cv2.putText(stopped_screen, stopped_text, (text_x, 240), cv2.FONT_HERSHEY_SIMPLEX, 1, (255, 255, 255), 2)
    
    manual_screen = np.zeros((480, 640, 3), dtype=np.uint8)
    manual_text = "Current State: MANUAL"
    (text_width, _), _ = cv2.getTextSize(manual_text, cv2.FONT_HERSHEY_SIMPLEX, 1, 2)
    text_x = (640 - text_width) // 2
    cv2.putText(manual_screen, manual_text, (text_x, 240), cv2.FONT_HERSHEY_SIMPLEX, 1, (255, 255, 255), 2)

    while True:
        display_frame = None
        if current_state == ControlState.CRUISE or current_state == ControlState.FOLLOW:
            display_frame = current_visual_frame.copy() # Display live vision data.
        elif current_state == ControlState.MANUAL:
            display_frame = manual_screen.copy() # Display manual mode status.
        elif current_state == ControlState.MAPPING:
            display_frame = current_visual_frame.copy() # Display mapping in progress screen.
        else: # ControlState.STOPPED
            display_frame = stopped_screen.copy() # Display stopped status.

        cv2.imshow(window_name, display_frame)

        # Check for 'q' key press to initiate program shutdown.
        if cv2.waitKey(1) & 0xFF == ord('q'):
            print("'q' pressed. Shutting down...")
            asyncio.get_running_loop().stop() # Stop the asyncio event loop.
            break
        
        await asyncio.sleep(0.03) # Approximately 30 FPS update rate.
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

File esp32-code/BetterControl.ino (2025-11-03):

#include <Wire.h>
#include <Adafruit_GFX.h>
#include <Adafruit_SH110X.h>
#include <BLEDevice.h>
#include <BLEServer.h>
#include <BLEUtils.h>
#include <BLE2902.h>

// 16x16 pixel wheelchair bitmap, stored in Flash memory
const unsigned char wheelchair_bmp[] PROGMEM = {
    0x00, 0x00, 0x01, 0x80, 0x03, 0xc0, 0x03, 0xc0, 0x07, 0xe0, 0x07, 0xe0, 0x1f, 0xf8, 0x3f, 0xfc, 
    0x3f, 0xfc, 0x1f, 0xf8, 0x0c, 0x30, 0x0c, 0x30, 0x1f, 0xf8, 0x38, 0x1c, 0x20, 0x04, 0x00, 0x00
};

// --- OLED Screen Configuration ---
#define SCREEN_WIDTH 128
#define SCREEN_HEIGHT 128
#define OLED_RESET -1
Adafruit_SH1107 display = Adafruit_SH1107(SCREEN_WIDTH, SCREEN_HEIGHT, &Wire, OLED_RESET, 400000, 0x3C);

// --- Pin Definitions (Updated with new understanding) ---
const int A_IN1_PIN = 34; // ValLeftX
const int A_IN2_PIN = 35; // ValRightX
const int A_IN3_PIN = 32; // ValDownY
const int A_IN4_PIN = 33; // ValupY
const int LED_GPIO = 4;
const int I2C_SDA_PIN = 22;
const int I2C_SCL_PIN = 23;
const int BUTTON_PIN = 21; // Emergency stop button

// --- BLE UUIDs ---
#define SERVICE_UUID           "c7a72f3e-3151-4d39-a18e-4a73426b3e2b"
#define CHARACTERISTIC_UUID_RX "f3711319-333e-41a4-b04b-32a7b8e1136c"
#define CHARACTERISTIC_UUID_TX "d1aea128-4f7e-4c4f-a7b5-c603a111a00a"

// --- Global Variables ---
BLEServer* pServer = NULL;
BLECharacteristic* pTxCharacteristic = NULL;
BLECharacteristic* pRxCharacteristic = NULL;
bool deviceConnected = false;
int wheelchairX = -16; 

// --- NEW: State Machine & Menu Variables ---
enum AppState {
    STATE_MENU,
    STATE_CONTROL
};
AppState currentState = STATE_MENU; // Start in the menu

// --- NEW: Sub-state for the menu ---
enum MenuState {
    MENU_STATE_MAIN,
    MENU_STATE_SUBPAGE // e.g., "About" or "Settings"
};
MenuState currentMenuState = MENU_STATE_MAIN;

const char* menuItems[] = {"Start Control", "Cruise Control", "Follow"};
const int numMenuItems = 3;
int selectedMenuItem = 0;
bool joyMoved = false; // Flag to prevent rapid scrolling

// --- NEW: Joystick Activation Threshold ---
// We now have 4 directional inputs, not 2 joysticks.
// We assume a resting value is low (e.g., < 1000) and an activated
// value is high (e.g., > 2300) when a direction is pressed.
#define JOY_ACTIVATION_THRESHOLD 2300 // The value to trigger a "press"

// --- Helper Function to Update OLED Display ---
void updateDisplay(const String& line1, const String& line2 = "", const String& line3 = "") {
    display.clearDisplay();
    display.setTextSize(1);
    display.setTextColor(SH110X_WHITE);
    display.setCursor(0, 0);
    display.println(line1);
    if (line2.length() > 0) {
        display.setCursor(0, 10);
        display.println(line2);
    }
    if (line3.length() > 0) {
        display.setCursor(0, 20);
        display.println(line3);
    }
    display.display();
}

// --- BLE Server Callbacks ---
class MyServerCallbacks: public BLEServerCallbacks {
    void onConnect(BLEServer* pServer) {
        deviceConnected = true;
        Serial.println("✅ Client Connected");
    }

    void onDisconnect(BLEServer* pServer) {
        deviceConnected = false;
        Serial.println("❌ Client Disconnected");
        pServer->getAdvertising()->start();
        Serial.println("📢 Advertising restarted...");
        // If we disconnect, force back to the menu
        currentState = STATE_MENU;
        currentMenuState = MENU_STATE_MAIN;
    }
};

// --- BLE Characteristic Callbacks ---
class MyCharacteristicCallbacks: public BLECharacteristicCallbacks {
    void onWrite(BLECharacteristic *pCharacteristic) {
        String rxValue = pCharacteristic->getValue();
        if (rxValue.length() > 0) {
            Serial.print("Received Value: ");
            Serial.println(rxValue);
            if (rxValue[0] == '1') {
                digitalWrite(LED_GPIO, HIGH);
            } else if (rxValue[0] == '0') {
                digitalWrite(LED_GPIO, LOW);
            }
        }
    }
};

// --- Emergency Stop Function ---
void emergencyStop() {
    Serial.println("🚨 Emergency STOP Activated!");
    
    // Force state to menu
    currentState = STATE_MENU;
    currentMenuState = MENU_STATE_MAIN;

    display.clearDisplay();
    display.setTextSize(2);
    display.setTextColor(SH110X_WHITE);
    display.setCursor(10, 50);
    display.println("Emergency");
    display.setCursor(40, 70);
    display.println("STOP");
    display.display();

    if (deviceConnected) {
        pTxCharacteristic->setValue("STOP");
        pTxCharacteristic->notify();
        Serial.println("Sent BLE message: STOP");
    }
    delay(2000);
    
    joyMoved = true; // Prevent accidental selection
}

// --- Function to draw the menu ---
void drawMenu() {
    display.clearDisplay();
    display.setTextSize(2); // Title size
    display.setTextColor(SH110X_WHITE);
    display.setCursor(10, 10);
    display.println("MAIN MENU");

    display.setTextSize(1); // Item size
    for (int i = 0; i < numMenuItems; i++) {
        display.setCursor(10, 40 + (i * 15));
        if (i == selectedMenuItem) {
            display.print("> "); // Selector
        } else {
            display.print("  ");
        }
        display.println(menuItems[i]);
    }
    display.display();
}
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

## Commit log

2025-09-02 Intial Commit
    [blender_viewer.blend]
2025-10-09 Shit new MPU
    [raw_scan_data.csv]
2025-10-25 Shit Code
    [raw_scan_data.csv, raw_scan_data_gyro.csv]
2025-10-30 Shitty esp32 code for menu and manual control
    GIT GIT
2025-11-02 mainflow test
    [raw_scan_data.csv]
2025-11-03 MVP made
    [point_cloud_map_20251103_161224.csv, raw_scan_data_20251103_160945.csv]
2025-11-03 Better BLE control menu with Cruise and Follow
    This file implements a BLE joystick control system for a wheelchair, including menu navigation and emergency stop functionality and adding the needed cruise control and follow commands
2025-11-08 Current MVP
2025-11-12 Cleanup Mainflow Bugs
    [raw_scan_data_20251110_160324.csv, raw_scan_data_20251110_161347.csv, raw_scan_data_20251110_184339.csv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]
2025-11-18 csv removal
    [point_cloud_map_20251103_161224.csv, raw_scan_data.csv, raw_scan_data_20251103_160945.csv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]
2025-11-19 Clean Up
    [blender_viewer.blend]
